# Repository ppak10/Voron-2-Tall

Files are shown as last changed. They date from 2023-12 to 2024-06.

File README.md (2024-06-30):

# Voron 2 Tall

<!-- <div align="center">
  <img src="./images/placeholder.JPEG" width="500px">
</div> -->

Collection of files for building custom Voron 2.4 with a build volume of 350 mm
x 350 mm x 930 mm (13.78 in x 13.78 in x 36.61 in) modified from the base LDO
Voron 2.4 Kit. 

## Mods
- [Cable Port Flush Mount Skirt](https://mods.vorondesign.com/details/3vEc5I965u0puzAmz9DqvA) - [ppak10](https://github.com/ppak10)
- [Enclosed Z-Chain Guide](https://mods.vorondesign.com/details/4mSRcdfNCvSq6nsRHETw) - [ppak10](https://github.com/ppak10)
- [Nevermore Micro](https://github.com/nevermore3d/Nevermore_Micro) - [nevermore3d](https://github.com/nevermore3d)
- [Purge Bucket](https://github.com/VoronDesign/VoronUsers/tree/main/orphaned_mods/edwardyeeks/Decontaminator_Purge_Bucket_%26_Nozzle_Scrubber) - [edwardyeeks](https://github.com/edwardyeeks)
- Umbilical Mount (Choose One) 
  - [Rear Umbilical](https://mods.vorondesign.com/details/ho9WEyf6msbGKhTbtM59mQ) - [Minsekt](https://github.com/Minsekt)
  - [PG7 Umbilical Mount](https://www.printables.com/model/312008-voron-24-a-drive-pg7-umbilical-mount) - [jphalip](https://www.printables.com/@jphalip)

- [Y Endstop Relocation](https://mods.vorondesign.com/details/ho9WEyf6msbGKhTbtM59mQ) - [Minsekt](https://github.com/Minsekt)

## Canbus Setup

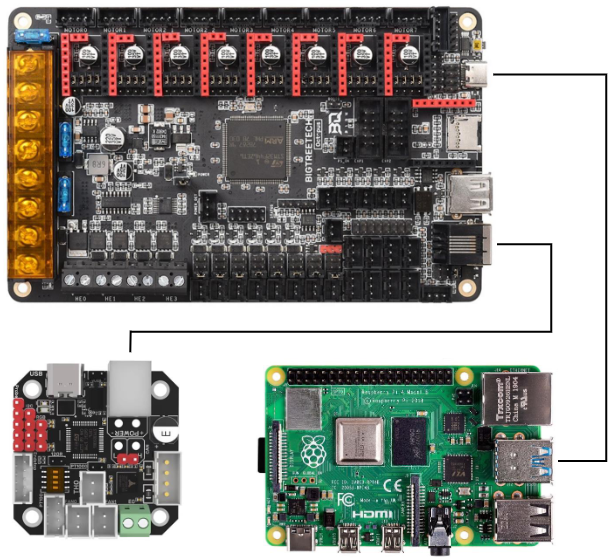
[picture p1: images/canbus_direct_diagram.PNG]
Canbus Direct Diagram


I mostly followed the steps outlined in this [forum post](https://www.teamfdm.com/forums/topic/672-how-to-use-can-toolhead-boards-connected-directly-to-octopus-octopus-pro-on-canboot/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) to connect EBB directly to
Octopus.

More specifically, I followed the guide this guide that was attached.

[**How to Use CAN Toolhead Boards Connected Directly to Octopus / Octopus Pro on CanBoot**](Manuals/Canbus/How%20to%20Use%20CAN%20Toolhead%20Boards%20Connected%20Directly%20to%20Octopus.pdf)

### Notes
1. CanBoot has updated name to Katapult but instructions in manual should still work.
2. If `can0` doesn't automatically show up in `ifconfig` so this command should solve that:
    ```bash
    sudo ip link set can0 up type can bitrate 250000
    sudo ip link set can0 txqueuelen 128
    ```
3. Make sure the high and low can wires are set correctly otherwise ebb will not show up properly.

### Troubleshooting 
- [CANBus_Query.py not returning EBB36’s UUID. Setup: Pi 4, Octopus v1.1, EBB36 v1.2](https://klipper.discourse.group/t/canbus-query-py-not-returning-ebb36s-uuid-setup-pi-4-octopus-v1-1-ebb36-v1-2/8464)
- [MCU timer too close error](https://klipper.discourse.group/t/help-with-troubleshooting-mcu-timer-too-close-error/15913/18)
- [EBB_CAN](https://github.com/EricZimmerman/VoronTools/blob/main/EBB_CAN.md)

## Toolhead (Dragon Burner 2.85 mm)
[Dragon Burner V8](https://github.com/chirpy2605/voron/tree/main/V0/Dragon_Burner)
toolhead is used as the base for mounting an
[Orbiter F2.85 mm](https://www.orbiterprojects.com/orbiter-f2-85/) extruder and
[V6 All-Metal HotEnd](https://e3d-online.com/products/v6-all-metal-hotend?variant=40923457519675).

### Notes
1. Some printed component will need some light sanding to fit together properly.
    - Be gentle with the fan components, they can break easily.
2. Make sure to calibrate E-steps as the default settings will most likely result in under-extrusion.
    - Here's a [good guide](https://ellis3dp.com/Print-Tuning-Guide/articles/extruder_calibration.html) with instructions to calibrate E-steps
    - General Formula: `new_rotation_distance = previous_rotation_distance * (actual_extrude_distance / 100)`

### Extruder


- [Orbiter F2.85 mm Files](https://www.thingiverse.com/thing:4860182)

### Hotend
- [How To: Successfully Assemble an E3D v6 All-Metal HotEnd](https://www.matterhackers.com/articles/how-to-assemble-an-e3d-v6-all-metal-hotend)

## Other Useful Links

### LDO Docs
- [Wiring Guide](https://docs.ldomotors.com/en/voron/voron2/wiring_guide_rev_c)
- [Printed Parts](https://docs.ldomotors.com/en/voron/voron2/printed_part_guide_rev_c)

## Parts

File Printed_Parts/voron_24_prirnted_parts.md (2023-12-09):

### Voron 2.4 Printed Parts List
https://gist.github.com/cmidgley/10423bbae72dacb02c46926f60acb7d2

List of parts to print for [Voron 2.4](https://github.com/VoronDesign/Voron-2) organized by the [Assembly Manuals](https://github.com/VoronDesign/Voron-2/blob/Voron2.4/Docs/2.4_Assembly_Manual.pdf) order of assembly, allowing for just-in-time printing of parts while building the printer.  Configuration is standard Voron 2.4 (Afterburner Direct Feed, DIN rail mounts) with choices for E3D, Dragon or Mosquito hot ends on a 250mm, 300mm or 350mm frame.  No parts for the drag chain are included, as often these are purchased parts rather than printed.

Names of the sections (such as `Gantry/X_Axis/XY Joints`) match the name of the [STL directory](https://github.com/VoronDesign/Voron-2/tree/Voron2.4/STLs/VORON2.4) that contains the prints.  Note that Voron Design uses filenames starting with `[a]_` at the start of a filename to indicate parts that can be printed in an accent color.

_Credit to [krobertson](https://gist.github.com/krobertson/adfd96689e8b66e7e122705c9ac6bb21) for making a Gist of all parts. This Gist is a modified version of that list, organized by order of assembly, removed parts that don't need printing, identified parts that are optional or specific to a build, and fixed a few incorrect part listings._

--------------------------------------------------------------------------------

### Frame (page 10)

#### [Tools](https://github.com/VoronDesign/Voron-2/tree/Voron2.4/STLs/VORON2.4/Tools)

```
[  ]  [  ]   rail_installation_guide_center_x2.stl
```

--------------------------------------------------------------------------------

### Z Drive Assembly (page 18)

#### [Z_Drive](https://github.com/VoronDesign/Voron-2/tree/Voron2.4/STLs/VORON2.4/Z_Drive)

```
[  ]  [  ]   [a]_belt_tensioner_a_x2.stl
[  ]  [  ]   [a]_belt_tensioner_b_x2.stl
[  ]  [  ]   [a]_z_drive_baseplate_a_x2.stl
[  ]  [  ]   [a]_z_drive_baseplate_b_x2.stl
[  ]  [  ]   z_drive_main_a_x2.stl
[  ]  [  ]   z_drive_main_b_x2.stl
[  ]  [  ]   z_drive_retainer_a_x2.stl
[  ]  [  ]   z_drive_retainer_b_x2.stl
[  ]  [  ]   z_motor_mount_a_x2.stl
[  ]  [  ]   z_motor_mount_b_x2.stl
```

#### [Z_Idlers](https://github.com/VoronDesign/Voron-2/tree/Voron2.4/STLs/VORON2.4/Z_Idlers)

_There are two different GT20 20T pully files; only one set of them should be printed_

```
[  ]  [  ]  [  ]  [  ]   [a]_z_tensioner_x4_6mm.stl <- select one vvv (6mm pully)
[  ]  [  ]  [  ]  [  ]   [a]_z_tensioner_x4_9mm.stl <- select one ^^^ (9mm pully)
[  ]  [  ]               z_tensioner_bracket_a_x2.stl
[  ]  [  ]               z_tensioner_bracket_b_x2.stl
```

#### [Z_Endstop](https://github.com/VoronDesign/Voron-2/tree/Voron2.4/STLs/VORON2.4/Z_Endstop)

```
[  ]   nozzle_probe.stl
```

--------------------------------------------------------------------------------

### AB Drive Modules (page 38)

#### [Gantry/Front_Idlers](https://github.com/VoronDesign/Voron-2/tree/Voron2.4/STLs/VORON2.4/Gantry/Front_Idlers)

```
[  ]   [a]_tensioner_left.stl
[  ]   [a]_tensioner_right.stl
[  ]   front_idler_left_lower.stl
[  ]   front_idler_left_upper.stl
[  ]   front_idler_right_lower.stl
[  ]   front_idler_right_upper.stl
```

#### [Gantry/AB_Drive_Units](https://github.com/VoronDesign/Voron-2/tree/Voron2.4/STLs/VORON2.4/Gantry/AB_Drive_Units)

```
[  ]         [a]_cable_cover.stl
[  ]  [  ]   [a]_z_chain_retainer_bracket_x2.stl
[  ]         a_drive_frame_lower.stl
[  ]         a_drive_frame_upper.stl
[  ]         b_drive_frame_lower.stl
[  ]         b_drive_frame_upper.stl
```

--------------------------------------------------------------------------------

### Gantry (page 46)

#### [Gantry/X_Axis/XY Joints](https://github.com/VoronDesign/Voron-2/tree/Voron2.4/STLs/VORON2.4/Gantry/X_Axis/XY_Joints)

_Select one endstop_pod_* , and one xy_joint_cable_bridge_* depending on your hardware kit_

```
[  ]   [a]_endstop_pod_hall_effect.stl <- select one vvv (hall effect XY endstops)
[  ]   [a]_endstop_pod_microswitch.stl <- select one ^^^ (microswitch XY endstops)
[  ]   [a]_xy_joint_cable_bridge_generic.stl <= select one vvv (generic drag chain)
[  ]   [a]_xy_joint_cable_bridge_igus.stl    <= select one ^^^ (igus drag chain)
[  ]   xy_joint_left_lower.stl
[  ]   xy_joint_left_upper.stl
[  ]   xy_joint_right_lower.stl
[  ]   xy_joint_right_upper.stl
```

#### [Gantry](https://github.com/VoronDesign/Voron-2/tree/Voron2.4/STLs/VORON2.4/Gantry)

```
[  ]  [  ]  [  ]  [  ]   [a]_z_belt_clip_lower_x4.stl
[  ]  [  ]  [  ]  [  ]   [a]_z_belt_clip_upper_x4.stl
[  ]                     z_chain_bottom_anchor.stl
[  ]                     z_chain_guide.stl              <-- Not in CAD or documentation
```

--------------------------------------------------------------------------------

### Afterburner (page 58)

#### [Gantry/X_Axis/X Carriage](https://github.com/VoronDesign/Voron-2/tree/Voron2.4/STLs/VORON2.4/Gantry/X_Axis/X_Carriage)

```
[  ]  [  ]   [a]_belt_clamp_x2.stl
[  ]         [a]_blower_housing_front.stl
[  ]         blower_housing_rear.stl
[  ]         hotend_fan_mount.stl
[  ]         probe_retainer_bracket.stl
[  ]         x_carriage_frame_left.stl
[  ]         x_carriage_frame_right.stl
[  ]         x_carriage_pivot_block.stl
```

#### [Gantry/X_Axis/X Carriage/Printheads/E3D V6](https://github.com/VoronDesign/Voron-2/tree/Voron2.4/STLs/VORON2.4/Gantry/X_Axis/X_Carriage/Printheads/E3D_V6)

_Select only one printhead; this is for E3D_

```
[  ]   printhead_front_e3dv6.stl
[  ]   printhead_rear_e3dv6.stl
```

#### [Gantry/X_Axis/X Carriage/Printheads/Slice Mosquito](https://github.com/VoronDesign/Voron-2/tree/Voron2.4/STLs/VORON2.4/Gantry/X_Axis/X_Carriage/Printheads/Slice_Mosquito)

_Select only one printhead; this is for Slice Mosquito_

```
[  ]   printhead_front_mosquito.stl
[  ]   printhead_rear_mosquito.stl
```

#### [Gantry/X_Axis/X Carriage/Printheads/TriangleLab Dragon](https://github.com/VoronDesign/Voron-2/tree/Voron2.4/STLs/VORON2.4/Gantry/X_Axis/X_Carriage/Printheads/TriangleLab_Dragon)

_Select only one printhead; this is for Phaetus Dragon_

```
[  ]   printhead_front_dragon.stl
[  ]   printhead_rear_dragon.stl
```

#### [Gantry/X_Axis/X Carriage/Direct Feed](https://github.com/VoronDesign/Voron-2/tree/Voron2.4/STLs/VORON2.4/Gantry/X_Axis/X_Carriage/Direct_Feed)

_Select the chain anchor (generic or igus) that matches your drag chain choice_ 

```
[  ]   [a]_connector_cover.stl
[  ]   [a]_guidler.stl
[  ]   [a]_latch.stl
[  ]   chain_anchor_generic.stl <-- select one vvv (generic drag chain)
[  ]   chain_anchor_igus.stl    <-- select one ^^^ (igus drag chain)
[  ]   extruder_body.stl
[  ]   extruder_motor_plate.stl
[  ]   latch_shuttle.stl
```

--------------------------------------------------------------------------------

### Belting Z Drive (page 78)

#### [Gantry/Z_Joints](https://github.com/VoronDesign/Voron-2/tree/Voron2.4/STLs/VORON2.4/Gantry/Z_Joints)

```
[  ]  [  ]  [  ]  [  ]   z_joint_lower_x4.stl
[  ]                     z_joint_upper_hall_effect.stl <-- if using hall effect XY
[  ]  [  ]  [  ]  [  ]   z_joint_upper_x4.stl <-- use x3 if using hall effect XY
```

--------------------------------------------------------------------------------

###  LCD Module (page 82)

#### [Electronics_Compartment/LCD_Module](https://github.com/VoronDesign/Voron-2/tree/Voron2.4/STLs/VORON2.4/Electronics_Compartment/LCD_Module)

```
[  ]   [a]_mini12864_case_hinge.stl
[  ]   mini12864_case_front.stl
[  ]   mini12864_case_rear.stl
[  ]   mini12864_spacer.stl
```

--------------------------------------------------------------------------------

### Skirts (page 86)

#### [Electronics_Compartment/Plug_Panel](https://github.com/VoronDesign/Voron-2/tree/Voron2.4/STLs/VORON2.4/Electronics_Compartment/Plug_Panel)

```
[  ]   plug_panel_filtered_mains.stl
```

#### [Skirts](https://github.com/VoronDesign/Voron-2/tree/Voron2.4/STLs/VORON2.4/Skirts)

```
[  ]  [  ]   [a]_60mm_fan_blank_insert_x2.stl
[  ]  [  ]   [a]_belt_guard_a_x2.stl
[  ]  [  ]   [a]_belt_guard_b_x2.stl
[  ]  [  ]   side_fan_support_x2.stl
```

#### [250](https://github.com/VoronDesign/Voron-2/tree/Voron2.4/STLs/VORON2.4/Skirts/250)

_Use these skirts when printing a 250mm frame_

```
[  ]  [  ]   front_rear_skirt_a_250_x2.stl
[  ]  [  ]   front_rear_skirt_b_250_x2.stl
[  ]  [  ]   side_skirt_a_250_x2.stl
[  ]  [  ]   side_skirt_b_250_x2.stl
```

#### [300](https://github.com/VoronDesign/Voron-2/tree/Voron2.4/STLs/VORON2.4/Skirts/300)

_Use these skirts when printing a 300mm frame_

```
[  ]  [  ]   front_rear_skirt_a_300_x2.stl
[  ]  [  ]   front_rear_skirt_b_300_x2.stl
[  ]  [  ]   side_skirt_a_300_x2.stl
[  ]  [  ]   side_skirt_b_300_x2.stl
```

#### [350](https://github.com/VoronDesign/Voron-2/tree/Voron2.4/STLs/VORON2.4/Skirts/350)

_Use these skirts when printing a 350mm frame_

```
[  ]  [  ]   front_rear_skirt_a_350_x2.stl
[  ]  [  ]   front_rear_skirt_b_350_x2.stl
[  ]  [  ]   side_skirt_a_350_x2.stl
[  ]  [  ]   side_skirt_b_350_x2.stl
```

--------------------------------------------------------------------------------

### Panels (page 94)

#### [Panel_Mounting/Front_Doors](https://github.com/VoronDesign/Voron-2/tree/Voron2.4/STLs/VORON2.4/Panel_Mounting/Front_Doors)

```
[  ]  [  ]  [  ]  [  ]   door_hinge_x4.stl
[  ]  [  ]               handle_a_x2.stl
[  ]  [  ]               handle_b_x2.stl
[  ]  [  ]               latch_x2.stl
```

#### [Panel_Mounting](https://github.com/VoronDesign/Voron-2/tree/Voron2.4/STLs/VORON2.4/Panel_Mounting)

```
[  ]  [  ]  [  ]  [  ]                                                   bottom_panel_clip_x4.stl
[  ]  [  ]                                                               bottom_panel_hinge_x2.stl
[  ]  [  ]  [  ]  [  ]  [  ]  [  ]  [  ]  [  ]  [  ]  [  ]  [  ]  [  ]   corner_panel_clip_3mm_x12.stl  <-- 3mm no foam, 6mm w/foam
[  ]  [  ]  [  ]  [  ]                                                   corner_panel_clip_6mm_x4.stl   <-- print either the 3mm or
[  ]  [  ]  [  ]  [  ]  [  ]  [  ]  [  ]  [  ]  [  ]  [  ]  [  ]  [  ]   midspan_panel_clip_3mm_x12.stl <-- the 6mm set 
[  ]  [  ]  [  ]                                                         midspan_panel_clip_6mm_x3.stl  <--  
[  ]  [  ]                                                               z_belt_cover_a_x2.stl
[  ]  [  ]                                                               z_belt_cover_b_x2.stl
```

--------------------------------------------------------------------------------

### Spool Holder (page 102)

#### [Spool_Management](https://github.com/VoronDesign/Voron-2/tree/Voron2.4/STLs/VORON2.4/Spool_Management)

```
[  ]   bowen_retainer.stl
[  ]   spool_holder.stl
```

--------------------------------------------------------------------------------

### Exhaust Filter (page 106)

#### [Exhaust_Filter](https://github.com/VoronDesign/Voron-2/tree/Voron2.4/STLs/VORON2.4/Exhaust_Filter)

```
[  ]         [a]_filter_access_cover.stl
[  ]  [  ]   [a]_exhaust_filter_mount_x2.stl
[  ]         exhaust_filter_grill.stl
[  ]         exhaust_filter_housing.stl
```

--------------------------------------------------------------------------------

### Electronics Mounting (page 112)

#### [Electronics_Compartment/DIN_Brackets](https://github.com/VoronDesign/Voron-2/tree/Voron2.4/STLs/VORON2.4/Electronics_Compartment/DIN_Brackets)

_There are a number of different brackets here depending on your electronics selection._

```
[  ]  [  ]         duet_duex_bracket_x2.stl
[  ]               lrs_psu_bracket_clip.stl
[  ]  [  ]  [  ]   pcb_din_clip_x3.stl
[  ]  [  ]         ramps_bracket_x2.stl
[  ]               raspberrypi_bracket.stl
[  ]               rs25_psu_bracket_clip.stl
[  ]  [  ]         skr_1.3_bracket_x2.stl
[  ]  [  ]         skr_mini_e2_bracket_x2.stl
[  ]  [  ]         skr_mini_e3_bracket_x2.stl
```

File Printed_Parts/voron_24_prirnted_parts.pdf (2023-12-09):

voron_24_prirnted_parts.md | 2023-12-09

### Voron 2.4 Printed Parts List

https://gist.github.com/cmidgley/10423bbae72dacb02c46926f60acb7d2

List of parts to print for Voron 2.4 (https://github.com/VoronDesign/Voron-2) organized by the Assembly Manuals (https://github.com/VoronDesign/Voron-2/blob/Voron2.4/Docs/2.4_Assembly_Manual.pdf) order of assembly, allowing for just-in-time printing of parts while building the printer. Configuration is standard Voron 2.4 (Afterburner Direct Feed, DIN rail mounts) with choices for E3D, Dragon or Mosquito hot ends on a 250mm, 300mm or 350mm frame. No parts for the drag chain are included, as often these are purchased parts rather than printed.

Names of the sections (such as Gantry/X_Axis/XY Joints) match the name of the STL directory (https://github.com/VoronDesign/Voron-2/tree/Voron2.4/STLs/VORON2.4) that contains the prints. Note that Voron Design uses filenames starting with [a]_ at the start of a filename to indicate parts that can be printed in an accent color.

Credit to krobertson (https://gist.github.com/krobertson/adfd96689e8b66e7e122705c9ac6bb21) for making a Gist of all parts. This Gist is a modified version of that list, organized by

order of assembly, removed parts that don't need printing, identified parts that are optional or specific to a

build, and fixed a few incorrect part listings.

### Frame (page 10)

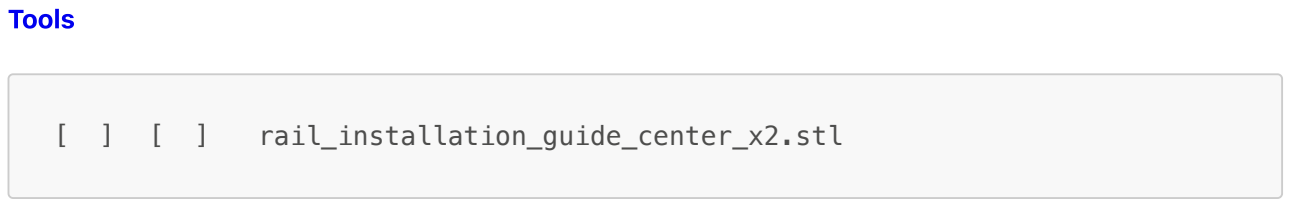
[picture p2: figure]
Tools; rail_installation_guide_center_x2.stl

### Z Drive Assembly (page 18)

Z_Drive (https://github.com/VoronDesign/Voron-2/tree/Voron2.4/STLs/VORON2.4/Z_Drive)

[ ] [ ] | [a]_belt_tensioner_a_x2.stl
[ ] [ ] | [a]_belt_tensioner_b_x2.stl
[ ] [ ] | [a]_z_drive_baseplate_a_x2.stl
[ ] [ ] | [a]_z_drive_baseplate_b_x2.stl
[ ] [ ] | z_drive_main_a_x2.stl
[ ] [ ] | z_drive_main_b_x2.stl
[ ] [ ] | z_drive_retainer_a_x2.stl
[ ] [ ] | z_drive_retainer_b_x2.stl
[ ] [ ] | z_motor_mount_a_x2.stl
[ ] [ ] | z_motor_mount_b_x2.stl

Z_Idlers (https://github.com/VoronDesign/Voron-2/tree/Voron2.4/STLs/VORON2.4/Z_Idlers)

There are two different GT20 20T pully files; only one set of them should be printed

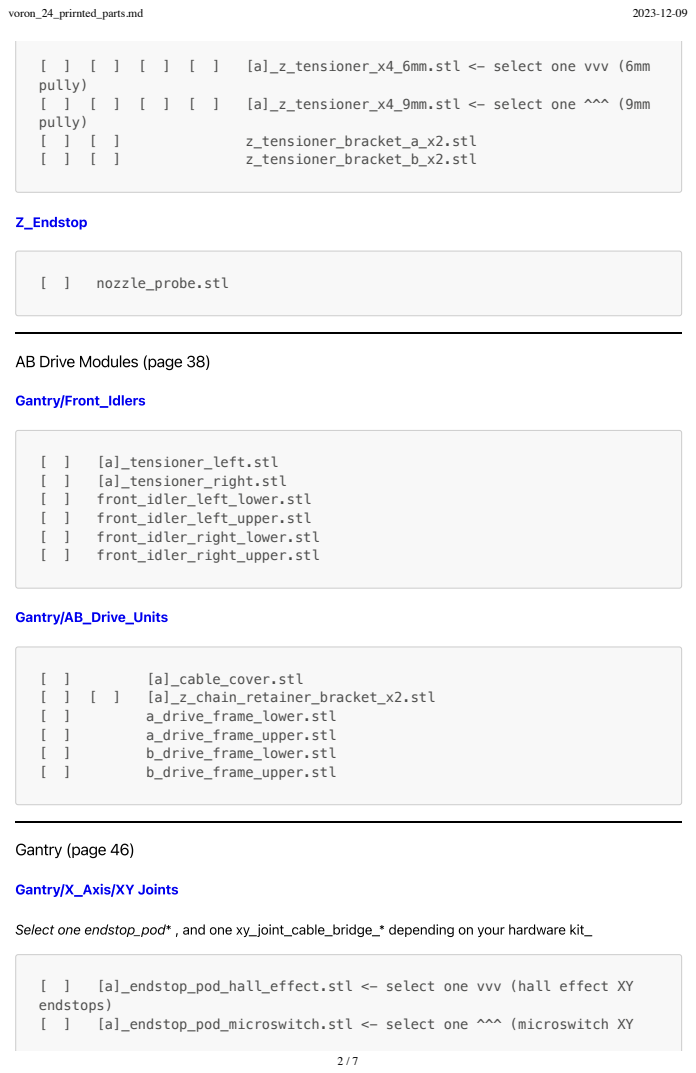
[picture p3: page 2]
[a]_z_tensioner_x4_6mm.stl <- select one vvv (6mm; pully); [a]_z_tensioner_x4_9mm.stl <- select one ^^^ (9mm; z_tensioner_bracket_a_x2.stl; z_tensioner_bracket_b_x2.stl; Z_Endstop; nozzle_probe.stl; Gantry/Front_Idlers; [a]_tensioner_left.stl; [a]_tensioner_right.stl; front_idler_left_lower.stl; front_idler_left_upper.stl; front_idler_right_lower.stl; front_idler_right_upper.stl; Gantry/AB_Drive_Units; [a]_cable_cover.stl; [a]_z_chain_retainer_bracket_x2.stl; a_drive_frame_lower.stl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

AB Drive Modules (page 38)

Gantry/X_Axis/XY Joints (https://github.com/VoronDesign/Voron-2/tree/Voron2.4/STLs/VORON2.4/Gantry/X_Axis/XY_Joints)

Select one endstop_pod* , and one xy_joint_cable_bridge_* depending on your hardware kit_

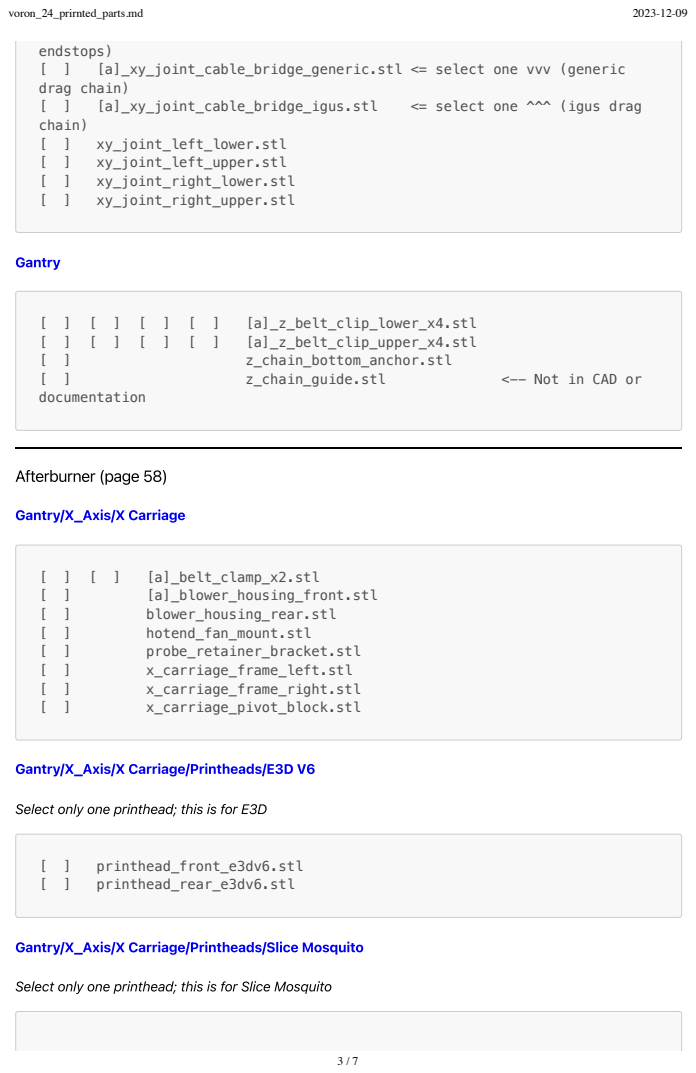
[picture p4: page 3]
endstops); [a]_xy_joint_cable_bridge_generic.stl <= select one vvv (generic; drag chain); [a]_xy_joint_cable_bridge_igus.stl; <= select one ^^^ (igus drag; chain); xy_joint_left_lower.stl; xy_joint_left_upper.stl; xy_joint_right_lower.stl; xy_joint_right_upper.stl; Gantry; [a]_z_belt_clip_lower_x4.stl; [a]_z_belt_clip_upper_x4.stl; z_chain_bottom_anchor.stl; z_chain_guide.stl; <-- Not in CAD or; documentation; Afterburner (page 58); Gantry/X_Axis/X Carriage; [a]_belt_clamp_x2.stl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

Gantry/X_Axis/X Carriage/Printheads/E3D V6 (https://github.com/VoronDesign/Voron-2/tree/Voron2.4/STLs/VORON2.4/Gantry/X_Axis/X_Carriage/Printheads/E3D_V6)

Select only one printhead; this is for E3D

Gantry/X_Axis/X Carriage/Printheads/Slice Mosquito (https://github.com/VoronDesign/Voron-2/tree/Voron2.4/STLs/VORON2.4/Gantry/X_Axis/X_Carriage/Printheads/Slice_Mosquito)

Select only one printhead; this is for Slice Mosquito

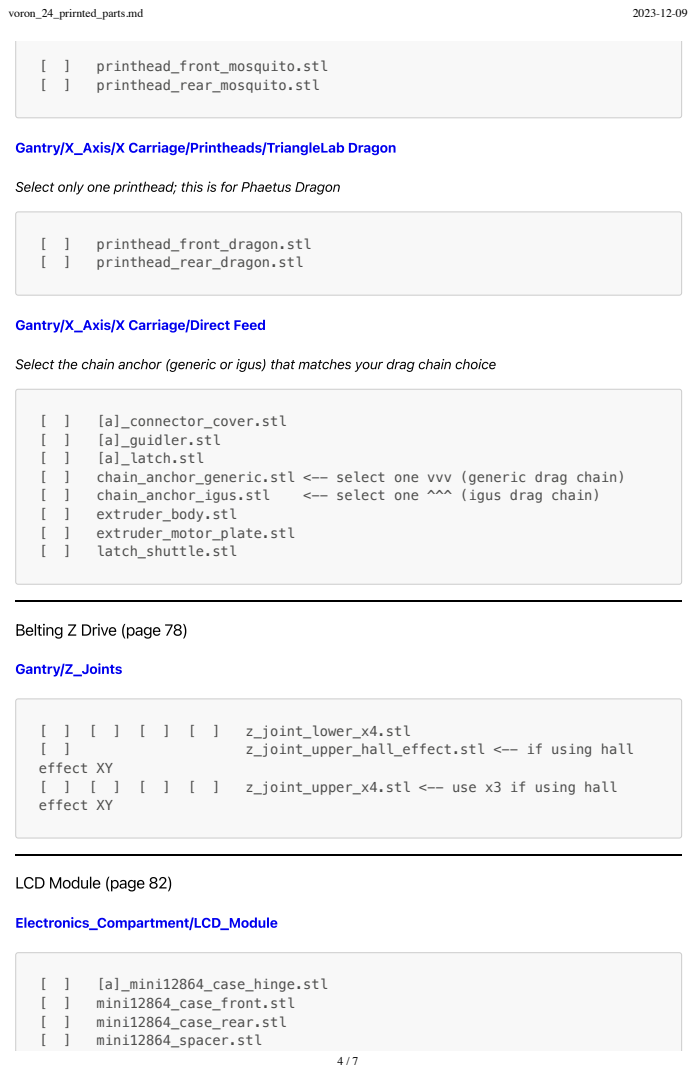
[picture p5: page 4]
printhead_front_mosquito.stl; printhead_rear_mosquito.stl; printhead_front_dragon.stl; printhead_rear_dragon.stl; [a]_connector_cover.stl; [a]_guidler.stl; [a]_latch.stl; chain_anchor_generic.stl <-- select one vvv (generic drag chain); chain_anchor_igus.stl; <-- select one ^^^ (igus drag chain); extruder_body.stl; extruder_motor_plate.stl; latch_shuttle.stl; Gantry/Z_Joints; z_joint_lower_x4.stl; z_joint_upper_hall_effect.stl <-- if using hall; effect XY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

Gantry/X_Axis/X Carriage/Printheads/TriangleLab Dragon (https://github.com/VoronDesign/Voron-2/tree/Voron2.4/STLs/VORON2.4/Gantry/X_Axis/X_Carriage/Printheads/TriangleLab_Dragon)

Select only one printhead; this is for Phaetus Dragon

Gantry/X_Axis/X Carriage/Direct Feed (https://github.com/VoronDesign/Voron-2/tree/Voron2.4/STLs/VORON2.4/Gantry/X_Axis/X_Carriage/Direct_Feed)

Select the chain anchor (generic or igus) that matches your drag chain choice

Belting Z Drive (page 78)

LCD Module (page 82)

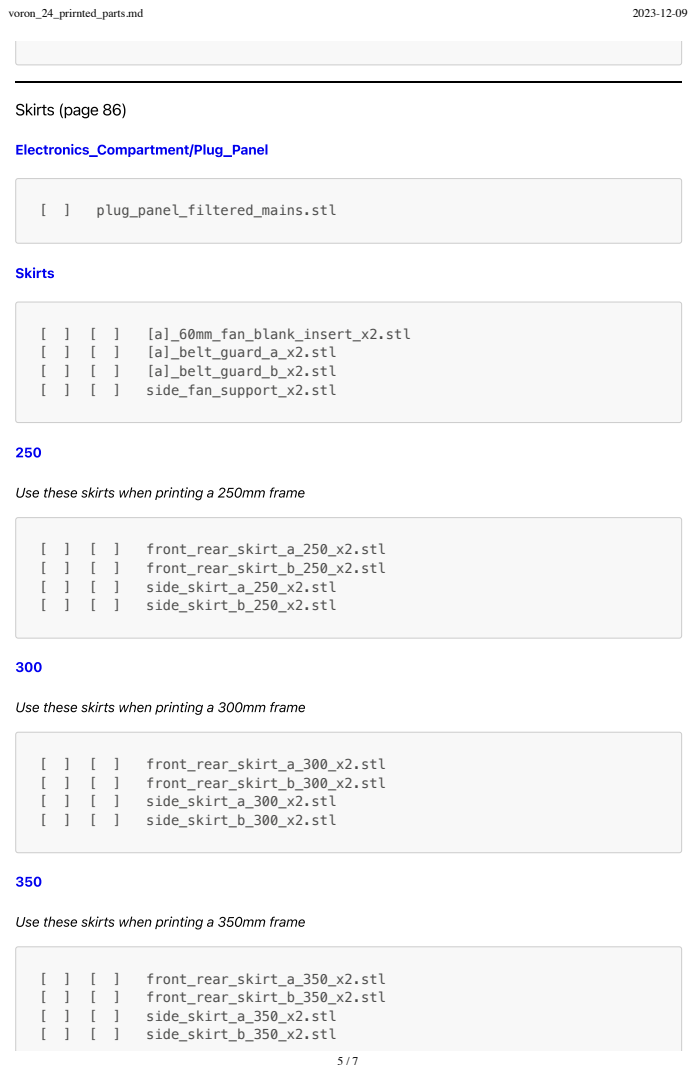
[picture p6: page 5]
Skirts (page 86); Electronics_Compartment/Plug_Panel; plug_panel_filtered_mains.stl; Skirts; [a]_60mm_fan_blank_insert_x2.stl; [a]_belt_guard_a_x2.stl; [a]_belt_guard_b_x2.stl; side_fan_support_x2.stl; front_rear_skirt_a_250_x2.stl; front_rear_skirt_b_250_x2.stl; side_skirt_a_250_x2.stl; side_skirt_b_250_x2.stl; front_rear_skirt_a_300_x2.stl; front_rear_skirt_b_300_x2.stl; side_skirt_a_300_x2.stl; side_skirt_b_300_x2.stl; front_rear_skirt_a_350_x2.stl; front_rear_skirt_b_350_x2.stl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

Use these skirts when printing a 250mm frame

Use these skirts when printing a 300mm frame

Use these skirts when printing a 350mm frame

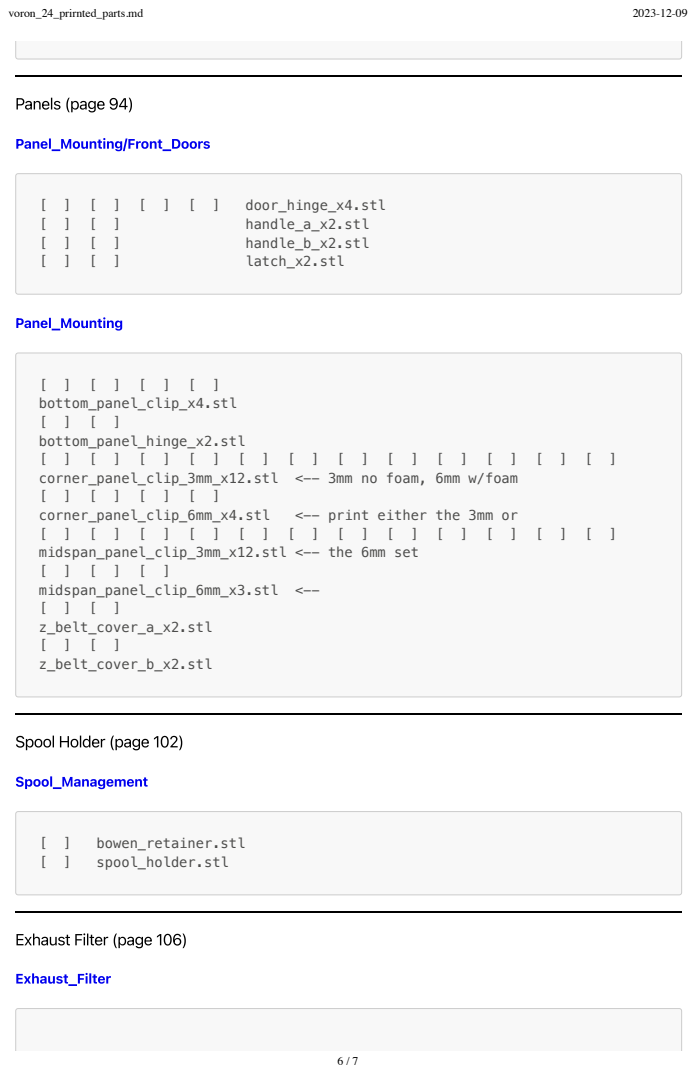
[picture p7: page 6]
Panels (page 94); Panel_Mounting/Front_Doors; door_hinge_x4.stl; handle_a_x2.stl; handle_b_x2.stl; latch_x2.stl; Panel_Mounting; [ ] [ ] [ ] [ ] bottom_panel_clip_x4.stl [ ] [ ] bottom_panel_hinge_x2.stl [ ] [ ] [ ] [ ] [ ] [ ] [ ] [ ] [ ] [ ] [ ] [ ] corner_panel_clip_3mm_x12.stl <-- 3mm no foam, 6mm w/foam [ ] [ ] [ ] [ ]; corner_panel_clip_6mm_x4.stl; <-- print either the 3mm or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

Spool Holder (page 102)

Exhaust Filter (page 106)

[ ] | [a]_filter_access_cover.stl
[ ] [ ] | [a]_exhaust_filter_mount_x2.stl
[ ] | exhaust_filter_grill.stl
[ ] | exhaust_filter_housing.stl

### Electronics Mounting (page 112)

Electronics_Compartment/DIN_Brackets (https://github.com/VoronDesign/Voron-2/tree/Voron2.4/STLs/VORON2.4/Electronics_Compartment/DIN_Brackets)

There are a number of different brackets here depending on your electronics selection.

[ ] [ ] | duet_duex_bracket_x2.stl
[ ] | lrs_psu_bracket_clip.stl
[ ] [ ] [ ] | pcb_din_clip_x3.stl
[ ] [ ] | ramps_bracket_x2.stl
[ ] | raspberrypi_bracket.stl
[ ] | rs25_psu_bracket_clip.stl
[ ] [ ] | skr_1.3_bracket_x2.stl
[ ] [ ] | skr_mini_e2_bracket_x2.stl
[ ] [ ] | skr_mini_e3_bracket_x2.stl

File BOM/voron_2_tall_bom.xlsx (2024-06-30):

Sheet: 1_custom_kit
1. LDO Kit + Custom Materials
Build Volume: 350mm x 350mm x (850mm to 930mm)
Frame Dimensions: 510mm x 510mm x 1130mm
 |  |  |  | Quantity |  |  | Subtotals
Description | Min Qty | Notes | Price | Desired | Ordered | Paid | Expected | Remaining | Link
LDO Voron 2.4 R2 (Rev C) 3D Printer Kit | 1 | Base Voron 2.4 Materials | $1449.00 | 1 | 0 | $0.00 | $1449.00 | $1449.00 | https://www.matterhackers.com/store/l/voron-design-corexy-fdm-3d-printer
M3-0.5 x 8mm Socket Head Cap Screws Bolts | 100 | Pack of 100 | $5.99 | 1 | 0 | $0.00 | $5.99 | $5.99 | https://www.amazon.com/dp/B09B2CGW12?psc=1&ref=ppx_yo2ov_dt_b_product_details
M3 Post-install T-nut | 163 | 20-m3 100pcs | $12.88 | 2 | 0 | $0.00 | $25.76 | $25.76 | https://www.aliexpress.us/item/2251832618848960.html?sk=KUHCwnu4&terminal_id=77b480c9601746d1be2247846d74a043
GT2 Open Belt LL-2GT-9 (9mm wide) - 8M | 1 | LDO Kit already includes 5.9M | $30.91 | 1 | 0 | $0.00 | $30.91 | $30.91 | https://www.aliexpress.us/item/2251832667244886.html?gatewayAdapt=glo2usa4itemAdapt
Linear Rail MGN9H 1000mm | 4 |  | $66 | 4 | 0 | $0.00 | $264.00 | $264.00 | https://3dprintingusa.com/products/9mm-linear-rail-1000mm-with-one-mgn9h-block
Misumi HFSB5-2020-1130-LCP-RCP | 4 | Holes 10mm from each end | $25.97 | 4 | 0 | $0.00 | $103.88 | $103.88 | https://us.misumi-ec.com/vona2/detail/110302683830/?Inch=0&Tab=preview
PTFE Tube (4mm OD 3mm ID) - 1000mm | 1 | 9.84 ft | $8.99 | 1 | 0 | $0.00 | $8.99 | $8.99 | https://www.amazon.com/gp/product/B07B8CK8L9/ref=ppx_yo_dt_b_asin_title_o00_s00?ie=UTF8&th=1
IGUS E2-15-10-028-0 Chain (1145mm [3.76ft]) | 1 | Extra (60) Chain Links for height | $46.44 | 1 | 0 | $0.00 | $46.44 | $46.44 | https://www.igus.com/iPro/iPro_01_0002_0015_USen.htm?ArtNr=E2-15-10-028-0&c=US&l=en
IGUS E2-150-10-12PZ Chain Ends (set) | 1 |  | $6.12 | 1 | 0 | $0.00 | $6.12 | $6.12 | https://www.igus.com/iPro/iPro_01_0002_0015_USen.htm?ArtNr=E2-15-10-028-0&c=US&l=en
Clear Acrylic Sheet 24" x 48" x 1/8"(4 Pack) | 1 | Side and Back Panels (483x1103x3 mm) | $139.80 | 1 | 0 | $0.00 | $139.80 | $139.80 | https://www.amazon.com/dp/B0BBQ7683N/ref=twister_B0BBQ7G8WZ?_encoding=UTF8&th=1
 |  | Door Panels (241.5x1103x3 mm) |  |  |  | $0.00
 |  |  |  |  |  | $0.00 | $2080.89 | $2080.89
Panels
Buildplate

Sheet: 2_wiring
2. Wiring
Necessary Materials
Option 1: Extended LDO Wiring
Option 2: Canbus (Recommended)
Necessary Materials |  |  |  | Quantity |  |  | Subtotals
Description | Min Qty | Notes | Price | Desired | Ordered | Paid | Expected | Remaining | Link
Female 4P to Male 4P Motor Extension Wire | 2 | For A/B stepper and limit (Pack of 2) | $12.99 | 2 | 0 | $0.00 | $25.98 | $25.98 | https://www.amazon.com/dp/B098J4MM3G?psc=1&ref=ppx_yo2ov_dt_b_product_details
Heat Shrink Tubing & Sleeves Pre-Cut Multi-Colored Heat Shrink Pack | 1 | Various heatshrink for extenders | $9.95 | 1 | 0 | $0.00 | $9.95 | $9.95 | https://www.mouser.com/ProductDetail/485-4559
 |  |  |  |  |  | $0.00 | $35.93 | $35.93
Option 1: Extended LDO Wiring |  |  |  | Quantity |  |  | Remaining Subtotals
Description | Min Qty | Notes | Price | Desired | Ordered | Paid | Required | Overall | Link
MicroFit3 Female Pin | 28 | For 20 - 24 AWG | $0.08 | 100 | 0 | $0.00 | $8.30 | $8.30 | https://www.mouser.com/ProductDetail/538-43030-0001-CT
MicroFit3 Connector Plug 14 Position | 2 | LDO toolhead plug | $1.02 | 2 | 0 | $0.00 | $2.04 | $2.04 | https://www.mouser.com/ProductDetail/538-43025-1410
Headers & Wire Housings PLUG FREE HNG 2P SINGLE ROW | 1 | Stealthburner RGB Extender (Female) | $0.38 | 2 | 0 | $0.00 | $0.76 | $0.76 | https://www.mouser.com/ProductDetail/Molex/43640-0201?qs=HlEFOAM0q6WaYhPmKKx%252BhQ%3D%3D
Headers & Wire Housings RECEPTACLE 2 POS SINGLE ROW | 1 | Stealthburner RGB Extender (Male) | $0.40 | 2 | 0 | $0.00 | $0.80 | $0.80 | https://www.mouser.com/ProductDetail/Molex/43645-0200?qs=4XSMV6Twtb2TZ7elJDViLw%3D%3D
Headers & Wire Housings 14CKT PLUG HSG FREE HANGING DR | 1 | Stealthburner Extender (Female) | $0.86 | 2 | 0 | $0.00 | $1.72 | $1.72 | https://www.mouser.com/ProductDetail/538-43020-1401
Headers & Wire Housings MicroFit Recep HSG DR 14Ckt GW BLK | 1 | Stealthburner Extender (Male) | $1.02 | 2 | 0 | $0.00 | $2.04 | $2.04 | https://www.mouser.com/ProductDetail/538-43025-1410
Headers & Wire Housings MALE 20-24 AWG BULK tin | 16 | Crimps for female molex sockets | $0.12 | 100 | 0 | $0.00 | $12.20 | $12.20 | https://www.mouser.com/ProductDetail/538-43031-0007
Headers & Wire Housings FEMALE TERM 20-24 | 16 | Crimps for male molex sockets | $0.11 | 100 | 0 | $0.00 | $11.40 | $11.40 | https://www.mouser.com/ProductDetail/Molex/43030-0007?qs=MuwpYaHj75276x2HQaDYIw%3D%3D
Hook-up Wire 24AWG7/32 PTFE 100ft SPOOL WHT | 1 | PTFE wire stealhburner extenders | $89.54 | 1 | 0 | $0.00 | $89.54 | $89.54 | https://www.mouser.com/ProductDetail/602-5854-7-100-01
Educational Kits JST connector Kit (2.54mm) | 1 | JST connectors for trimming cables | $8.90 | 1 | 0 | $0.00 | $8.90 | $8.90 | https://www.mouser.com/ProductDetail/426-FIT0255
 |  |  |  |  |  | $0.00 | $137.70 | $137.70
Option 2: Canbus (Recommended) |  |  |  | Quantity |  |  | Remaining Subtotals
Description | Min Qty | Notes | Price | Desired | Ordered | Paid | Required | Overall | Link
Big Tree Tech EBB SB2209 | 1 | For Stealthburner | $39.99 | 1 | 0 | $0.00 | $39.99 | $39.99 | https://biqu.equipment/products/bigtreetech-ebb-sb2209-can-v1-0
U2C V2.1 | 0 | Can use RJ11 port on Octopus instead | $46.88 | 1 | 0 | $0.00 | $46.88 | $46.88 | https://biqu.equipment/products/bigtreetech-ebb-sb2209-can-v1-0?variant=40214284468322
30 PIN Wire + 100K NTC B3950 | 0 | Precrimped small wires (recommended) | $6.55 | 1 | 0 | $0.00 | $6.55 | $6.55 | https://biqu.equipment/products/bigtreetech-ebb-sb2209-can-v1-0?variant=40214285058146
25ft - 1/4 inch PET Expandable Braided Sleeving | 1 | Aesthetic covering for canbus wire | $8.99 | 1 | 0 | $0.00 | $8.99 | $8.99 | https://www.amazon.com/dp/B098NKKZ3B?psc=1&ref=ppx_yo2ov_dt_b_product_details
2PCS 1m 13# Steel Piano Music Wire | 1 | Pack of 2 | $5.99 | 1 | 0 | $0.00 | $5.99 | $5.99 | Amazon.com: Bstinay 2PCS 1m 13# Steel Piano Music Wire for Replacement of Broken Strings Dia 0.775mm Silver : Musical Instruments (https://www.amazon.com/Bstinay-Replacement-Broken-Strings-0-775mm/dp/B0C4NFLDRF)
Cable Connectors PG7 PG9 PG11 PG13.5 PG16 PG19 | 1 | PG7 is used | $12.99 | 1 | 0 | $0.00 | $12.99 | $12.99 | https://www.amazon.com/dp/B09Z26FF8B?ref=ppx_yo2ov_dt_b_product_details&th=1
 |  |  |  |  |  | $0.00 | $121.39 | $121.39
Panels
Buildplate

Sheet: 3_mods
3. Optional Modifications
1. Raspberry Pi 5
2. Dragon Burner V8 2.85mm Filament Toolhead
1. Raspberry Pi 5 |  |  |  | Quantity |  |  | Subtotals
Description | Min Qty | Notes | Price | Desired | Ordered | Paid | Expected | Remaining | Link
Raspberry Pi 5 (8 Gb) | 1 | Upgrade from included Raspberry Pi 4 | $80.00 | 1 | 0 | $0.00 | $80.00 | $80.00 | SC1112 Raspberry Pi | Mouser (https://www.mouser.com/ProductDetail/Raspberry-Pi/SC1112?qs=HoCaDK9Nz5c86n0i5EQ%2FPA%3D%3D)
Active Cooler | 1 | Necessary for Raspberry Pi 5 | $5.00 | 1 | 0 | $0.00 | $5.00 | $5.00 | SC1148 Raspberry Pi | Mouser (https://www.mouser.com/ProductDetail/Raspberry-Pi/SC1148?qs=HoCaDK9Nz5fqo0izK2taew%3D%3D)
BATIGE Micro HDMI Female & Type C 3.0 Female Flush Mount | 1 | Optional port access to Raspberry Pi | $15.99 | 1 | 0 | $0.00 | $15.99 | $15.99 | https://www.amazon.com/dp/B0C68HPHR2?psc=1&ref=ppx_yo2ov_dt_b_product_details
FFC / FPC Jumper Cables Raspberry Pi 5 FPC Cables - Display, 200mm | 1 | Display Cable for Raspberry Pi 5 | $1.00 | 1 | 0 | $0.00 | $1.00 | $1.00 | https://www.mouser.com/ProductDetail/358-SC1131
NVME Base for Raspberry Pi 5 | 1 | Allows for higher storage capacity | $14.36 | 1 | 0 | $0.00 | $14.36 | $14.36 | https://shop.pimoroni.com/products/nvme-base?variant=41219587178579
 |  |  |  |  |  | $0.00 | $116.35 | $116.35
2. Dragon Burner V8 2.85mm Filament Toolhead |  |  |  | Quantity |  |  | Subtotals
Description | Min Qty | Notes | Price | Desired | Ordered | Paid | Expected | Remaining | Link
Big Tree Tech EBB36 | 1 | Alternative canbus PCB | $29.99 | 1 | 0 | $0.00 | $29.99 | $29.99 | https://www.amazon.com/dp/B0CNXRZTKL?psc=1&ref=ppx_yo2ov_dt_b_product_details
22 AWG Black and Red Silicone Wire | 1 | Delivers power to PCB | $9.98 | 1 | 0 | $0.00 | $9.98 | $9.98 | https://www.amazon.com/gp/product/B077XBWX8V/ref=ppx_yo_dt_b_asin_title_o00_s00?ie=UTF8&psc=1
Ferrule Crimping Tool AWG 23-7 with 1900PCS Ferrules Kit | 1 | Crimping for hotend wiring | $23.98 | 1 | 0 | $0.00 | $23.98 | $23.98 | https://www.amazon.com/gp/product/B0CWP24SL5/ref=ppx_yo_dt_b_asin_title_o00_s00?ie=UTF8&psc=1
V6 All-Metal HotEnd | 1 | 2.85mm 24V Direct Drive | $45.39 | 1 | 0 | $0.00 | $45.39 | $45.39 | https://e3d-online.com/products/v6-all-metal-hotend?variant=40923457519675
40 x 40 x 10 mm Brushless Exhaust Cooler Printer Radiators | 2 | Side fans for cowl | $5.93 | 2 | 0 | $0.00 | $11.86 | $11.86 | https://www.aliexpress.us/item/2251832613009306.html
30 x 30 x 10 mm Dual Ball Bearing Brushless Car Lamp Cooling Fan | 1 | Pack of 2 | $8.54 | 1 | 0 | $0.00 | $8.54 | $8.54 | https://www.aliexpress.us/item/3256802670785330.html
Orbiter Extruder for 2.85/3.0MM Filament | 1 | Provided fully assembled | $56.90 | 1 | 0 | $0.00 | $56.90 | $56.90 | https://www.aliexpress.us/item/3256802594760158.html
Rainbow RGBW LEDs | 0 | Rainbow Barf | $5.88 | 1 | 0 | $0.00 | $5.88 | $5.88 | https://www.aliexpress.us/item/3256805225841575.html
FYSETC Sequins with RGB WS2812 3535 Bright RGB LED | 1 | Allows for higher storage capacity | $2.92 | 1 | 0 | $0.00 | $2.92 | $2.92 | https://www.aliexpress.us/item/3256805836898589.html
 |  |  |  |  |  | $0.00 | $195.44 | $195.44
Panels
Buildplate

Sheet: theme_white_orange
White and Orange Theme BOM
Note: Avoid using white ABS with Titanium Dioxide
Description | Min Qty | Notes | Price | Desired Qty | Ordered Qty | Remaining Subtotal | Link
White Drag Chain R18 10x11 Open | 2 | Replaces IGUS E2i-10-10-018-0 Chain | $7.24 | 2 | 0 | $14.48 | https://www.aliexpress.com/item/3256805618753942.html
White Drag Chain R28 10x15 Open | 2 | Replaces IGUS E2-15-10-028-0 Chain | $7.70 | 2 | 0 | $15.40 | https://www.aliexpress.com/item/3256805618753942.html
Orange Acrylic Sheet 36" x 24" x 1/8" (3mm) | 2 | Top and Base Panels (469x469x4 mm) | $24.95 | 2 | 0 | $49.90 | https://makerstock.com/products/orange-fluorescent-acrylic?variant=32575693357153
 |  | 24" x 24" x 1/8" would work here too
Orange Acrylic Sheet 24" x 48" x 1/8" (3mm) | 4 | Side and Back Panels (483x1103x4 mm) | $49.95 | 4 | 0 | $199.80 | https://makerstock.com/products/orange-fluorescent-acrylic?variant=40860284026977
 |  | Door Panels (241.5x1103x4 mm)
Natural PRO Series ABS Filament - 1.75mm (1kg) | 2 | For General Printed Parts (Whiteish Color) | $52.00 | 2 | 0 | $104.00 | https://www.matterhackers.com/store/l/pro-series-abs/sk/MGY429XU
Polymaker ABS Filament 1kg Orange | 1 | For Accented Printed Parts | $21.99 | 1 | 0 | $21.99 | https://www.amazon.com/dp/B09DKS7TFT?psc=1&ref=ppx_yo2ov_dt_b_product_details
Krylon I00500A07 12-Ounce Triple Thick Clear Glaze Aerosol Spray,High-Gloss (Pack of 2) | 2 | Protective coating over spray painted parts | $12.94 | 2 | 0 | $25.88 | https://www.amazon.com/Krylon-I00500A00-12-Ounce-Triple-Aerosol/dp/B0CFXJGNMV
Krylon K05545007 COLORmaxx Spray Paint and Primer for Indoor/Outdoor Use Gloss White 12 Oz | 8 | For Painting Extrusions, Fans, etc. | $6.04 | 8 | 0 | $48.32 | https://www.amazon.com/Krylon-K05545007-COLORmaxx-Spray-Aerosol/dp/B07LFWZ84M
 |  |  |  |  |  | $479.77
Panels
Buildplate

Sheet: reference_self_source
Self Source BOM (For Cost Comparison)
Build Volume (350mm x 350mm x 930mm)
Frame Dimensions (510mm x 510mm x 1130mm)
Category | Description | Min Qty | Notes | Custom | Price | Desired Qty | Ordered Qty | Base Subtotal | Custom Subtotal | Remaining Subtotal | Link
Fasteners | M5x40 SHCS | 22 |  | FALSE | $0.26 | 25 | 0 | $6.50 | $0.00 | $6.50 | https://www.boltdepot.com/Product-Details.aspx?product=6527
 | M5x30 BHCS | 22 |  | FALSE | $0.46 | 25 | 0 | $11.50 | $0.00 | $11.50 | https://www.boltdepot.com/Product-Details.aspx?product=15651
 | M5x16 BHCS | 35 |  | FALSE | $0.39 | 40 | 0 | $15.60 | $0.00 | $15.60 | https://www.boltdepot.com/Product-Details.aspx?product=15648
 | M5x10 BHCS | 35 |  | FALSE | $0.33 | 40 | 0 | $13.20 | $0.00 | $13.20 | https://www.boltdepot.com/Product-Details.aspx?product=15646
 | M5 Hexnut | 16 |  | FALSE | $0.06 | 30 | 0 | $1.80 | $0.00 | $1.80 | https://www.boltdepot.com/Product-Details.aspx?product=4785
 | M5 Post-install T-nut | 68 | 20-m5 100pcs | FALSE | $10.28 | 1 | 0 | $10.28 | $0.00 | $10.28 | https://www.aliexpress.us/item/2251832618848960.html?onelink_thrd=0.015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
 | M5 1mm Shim | 42 | Pack of 50 | FALSE | $8.62 | 1 | 0 | $8.62 | $0.00 | $8.62 | https://www.mcmaster.com/98055A099/
 | M4x6 BHCS | 7 |  | FALSE | $0.12 | 10 | 0 | $1.20 | $0.00 | $1.20 | https://www.boltdepot.com/Product-Details.aspx?product=18944
 | M4 Knurled Nut (DIN 466-B) | 4 |  | FALSE | $0.69 | 5 | 0 | $3.45 | $0.00 | $3.45 | https://www.aliexpress.us/item/3256803272722533.html?gatewayAdapt=glo2usa4itemAdapt
 | M3x40 SHCS | 30 |  | FALSE | $0.20 | 35 | 0 | $7.00 | $0.00 | $7.00 | https://www.boltdepot.com/Product-Details.aspx?product=6387
 | M3x30 SHCS | 25 |  | FALSE | $0.20 | 30 | 0 | $6.00 | $0.00 | $6.00 | https://www.boltdepot.com/Product-Details.aspx?product=13641
 | M3x20 SHCS | 22 |  | FALSE | $0.16 | 25 | 0 | $4.00 | $0.00 | $4.00 | https://www.boltdepot.com/Product-Details.aspx?product=13639
 | M3x16 SHCS | 20 |  | FALSE | $0.15 | 25 | 0 | $3.75 | $0.00 | $3.75 | https://www.boltdepot.com/Product-Details.aspx?product=13638
 | M3x12 SHCS | 41 |  | FALSE | $0.12 | 50 | 0 | $6.00 | $0.00 | $6.00 | https://www.boltdepot.com/Product-Details.aspx?product=13637
 | M3x10 FHCS | 4 |  | FALSE | $0.17 | 10 | 0 | $1.70 | $0.00 | $1.70 | https://www.boltdepot.com/Product-Details.aspx?product=13251
 | M3x6 FHCS | 8 |  | FALSE | $0.15 | 10 | 0 | $1.50 | $0.00 | $1.50 | https://www.boltdepot.com/Product-Details.aspx?product=13249
 | M3x8 SHCS | 247 |  | TRUE | $0.12 | 250 | 0 | $0.00 | $30.00 | $30.00 | https://www.boltdepot.com/Product-Details.aspx?product=13635
 | M3x6 BHCS | 11 |  | FALSE | $0.12 | 15 | 0 | $1.80 | $0.00 | $1.80 | https://www.boltdepot.com/Product-Details.aspx?product=13334
 | M3 Hexnut | 6 |  | FALSE | $0.06 | 10 | 0 | $0.60 | $0.00 | $0.60 | https://www.boltdepot.com/Product-Details.aspx?product=4783
 | M3 Post-install T-nut | 163 | 20-m3 100pcs | TRUE | $12.88 | 2 | 0 | $0.00 | $25.76 | $25.76 | https://www.aliexpress.us/item/2251832618848960.html?sk=KUHCwnu4&terminal_id=77b480c9601746d1be2247846d74a043
 | M3 Hammer Head T-nuts | 60 | 100 pieces | FALSE | $7.99 | 1 | 0 | $7.99 | $0.00 | $7.99 | https://www.amazon.com/dp/B07SDFCTD4/
 | M3 Washer | 3 |  | FALSE | $0.07 | 10 | 0 | $0.70 | $0.00 | $0.70 | https://www.boltdepot.com/Product-Details.aspx?product=4513
 | M3 Threaded Insert (M3x5x4) | 110 | 100 pieces | FALSE | $8.10 | 2 | 0 | $16.20 | $0.00 | $16.20 | https://www.aliexpress.us/item/2255800046543591.html
 | M2x10 Self-tapping Screw | 16 | 50 pieces | FALSE | $12.91 | 1 | 0 | $12.91 | $0.00 | $12.91 | https://www.mcmaster.com/99397A267/
Motion | GT2 80T Pulley (5mm ID 6mm W) | 4 | 4 pieces | FALSE | $32.99 | 1 | 0 | $32.99 | $0.00 | $32.99 | https://www.aliexpress.us/item/2251832596290407.html?gatewayAdapt=glo2usa4itemAdapt
 | GT2 20T Pulley (5mm ID 6mm W) | 3 | 3 pieces | FALSE | $8.99 | 1 | 0 | $8.99 | $0.00 | $8.99 | https://www.aliexpress.us/item/2251832539995194.html?gatewayAdapt=glo2usa4itemAdapt
 | GT2 20T Pulley (5mm ID 9mm W) | 4 | 5 pieces | FALSE | $15.99 | 1 | 0 | $15.99 | $0.00 | $15.99 | https://www.aliexpress.us/item/2251832464361177.html?gatewayAdapt=glo2usa4itemAdapt
 | GT2 16T Pulley (5mm ID 6mm W) | 4 | 5 pieces | FALSE | $9.99 | 1 | 0 | $9.99 | $0.00 | $9.99 | https://www.aliexpress.us/item/2251801558494240.html?gatewayAdapt=glo2usa4itemAdapt
 | GT2 20T Toothed Idler (5mm ID 6mm W) | 2 |  | FALSE | $1.99 | 2 | 0 | $3.98 | $0.00 | $3.98 | https://www.aliexpress.us/item/2251832539995194.html?gatewayAdapt=glo2usa4itemAdapt
 | GT2 20T Toothed Idler (5mm ID 9mm W) | 4 | 5 pieces | FALSE | $9.99 | 1 | 0 | $9.99 | $0.00 | $9.99 | https://www.aliexpress.us/item/2251832564177700.html?gatewayAdapt=glo2usa4itemAdapt
 | F695 Bearing | 20 | 10 pieces | FALSE | $4.19 | 2 | 0 | $8.38 | $0.00 | $8.38 | https://www.aliexpress.us/item/2251832814871526.html?gatewayAdapt=glo2usa4itemAdapt
 | 625 Bearing | 12 | 12 pieces | FALSE | $3.43 | 1 | 0 | $3.43 | $0.00 | $3.43 | https://www.aliexpress.us/item/2251832804890021.html?gatewayAdapt=glo2usa4itemAdapt
 | Ø5x60mm Shaft D Cut | 4 |  | FALSE | $0.99 | 4 | 0 | $3.96 | $0.00 | $3.96 | https://west3d.com/products/round-shafts-5x30mm-5x60mm?variant=41971073024212
 | Ø5x35mm Shaft (trim to size) | 1 |  | FALSE | $0.59 | 1 | 0 | $0.59 | $0.00 | $0.59 | https://west3d.com/products/round-shafts-5x30mm-5x60mm?variant=41971073024212
 | GT2 Belt Loop (6mm W) - 188mm | 4 | 5 pieces | FALSE | $4.99 | 1 | 0 | $4.99 | $0.00 | $4.99 | https://www.aliexpress.us/item/2255799847707082.html?gatewayAdapt=glo2usa4itemAdapt
 | GT2 Open Belt LL-2GT-9 (9mm wide) - 2400mm | 4 | Length 3M | TRUE | $13.80 | 5 | 0 | $0.00 | $69.00 | $69.00 | https://www.aliexpress.us/item/2251832667244886.html?gatewayAdapt=glo2usa4itemAdapt
 | BMG Extruder Components Kit | 1 |  | FALSE | $15.25 | 1 | 0 | $15.25 | $0.00 | $15.25 | https://www.aliexpress.us/item/2255799834871688.html
 | Linear Rail MGN9H 400mm | 2 | GS_MGN9-1H-B400 | FALSE | $15 | 2 | 0 | $30.00 | $0.00 | $30.00 | https://www.robotdigg.com/product/1314/Black-anodized-linear-rail-7,-9,-12-and-15
 | Linear Rail MGN9H 1000mm | 4 |  | TRUE | $66 | 4 | 0 | $0.00 | $264.00 | $264.00 | https://3dprintingusa.com/products/9mm-linear-rail-1000mm-with-one-mgn9h-block
 | Linear Rail MGN12H 400mm | 1 | GS_MGN12-1H-B400 | FALSE | $15 | 1 | 0 | $15.00 | $0.00 | $15.00 | https://www.robotdigg.com/product/1314/Black-anodized-linear-rail-7,-9,-12-and-15
 | GT2 Open Belt LL-2GT-6 (6mm wide) - 2000mm | 2 | Length 2M | FALSE | $6.20 | 3 | 0 | $18.60 | $0.00 | $18.60 | https://www.aliexpress.us/item/2251832667244886.html?gatewayAdapt=glo2usa4itemAdapt
Electronics | Omron D2F-01L Micro Switch | 3 |  | FALSE | $2.02 | 4 | 0 | $8.08 | $0.00 | $8.08 | https://www.digikey.com/en/products/detail/omron-electronics-inc-emc-div/D2F-01L/83264
 | Inductive Probe (See sourcing guide) | 1 |  | FALSE | $7.00 | 1 | 0 | $7.00 | $0.00 | $7.00 | https://www.aliexpress.us/item/2251832663198775.html?gatewayAdapt=glo2usa
 | Hotend Kit (24V) | 1 |  | FALSE |  |  | 0 | $0.00 | $0.00 | $0.00
 | 40x40x20 Centrifugal Fan (24V) | 1 | 2 pieces | FALSE | $23.64 | 1 | 0 | $23.64 | $0.00 | $23.64 | https://www.aliexpress.us/item/3256801278415934.html?gatewayAdapt=glo2usa4itemAdapt
 | 40x40x10 Axial Fan (24V) | 1 |  | FALSE | $16.12 | 1 | 0 | $16.12 | $0.00 | $16.12 | https://www.aliexpress.us/item/2251832540325686.html?gatewayAdapt=glo2usa4itemAdapt
 | Mini 12864 Display | 1 | Possibly Optional | FALSE | $13.42 | 1 | 0 | $13.42 | $0.00 | $13.42 | https://www.amazon.com/BIGTREETECH-Mini12864-Graphic-Display-Prusa-i3/dp/B08P5LXR86
 | ZF Rocker Switch DPST 16A ON-OFF | 1 |  | FALSE | $3.00 | 1 | 0 | $3.00 | $0.00 | $3.00 | https://www.mouser.com/ProductDetail/ZF/WRG32F2BBRLN
 | ↱ TycoElectronics 10EGG1-1 Filtered Power Inlet (NA/UK) | 1 | Single Fuse | FALSE | $20.40 | 1 | 0 | $20.40 | $0.00 | $20.40 | https://www.mouser.com/ProductDetail/TE-Connectivity-PB/10EGG1-1?qs=vcjNRp8H9z1CsIf%2F5OknUw%3D%3D
 | ↳ TycoElectronics 10EGG1-2 Filtered Power Inlet (EU) | 1 | Dual Fuse | FALSE | $21.43 | 0 | 0 | $0.00 | $0.00 | $0.00 | https://www.mouser.com/ProductDetail/TE-Connectivity-PB/10EGG1-2/?qs=vcjNRp8H9z2nhEkRL4AXYw%3D%3D
 | ↱ Medium Blow Fuse 5x20mm 4A (220V mains) | 2 | Europe | FALSE | $1.11 | 0 | 0 | $0.00 | $0.00 | $0.00 | https://www.digikey.com/en/products/detail/littelfuse-inc/0232004-MXP/778023
 | ↳ Medium Blow Fuse 5x20mm 8A (120v mains) | 2 | North America | FALSE | $1.11 | 2 | 0 | $2.22 | $0.00 | $2.22 | https://www.digikey.com/en/products/detail/littelfuse-inc/0232008-MXP/778029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
 | Keystone CAT6 Insert (Optional) | 1 | Include Tool | FALSE | $75.95 | 0 | 0 | $0.00 | $0.00 | $0.00 | https://www.amazon.com/EMS-easyJACK-CAT6A-Kit-Termination/dp/B09S17YX4T
 | 60x60x20 Fan (24V) | 3 | 3 pieces | FALSE | $18.00 | 1 | 0 | $18.00 | $0.00 | $18.00 | https://www.amazon.com/dp/B08577444D
 | Controller with 7+ Stepper outputs | 1 | BTT Octopus V1.1 | FALSE | $55.99 | 1 | 0 | $55.99 | $0.00 | $55.99 | https://www.amazon.com/BIGTREETECH-Direct-Octopus-Control-Supports/dp/B094Y77FQN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
 | ↳ USB Cable for selected controller | 1 | Included above | FALSE | $12.99 | 0 | 0 | $0.00 | $0.00 | $0.00 | https://www.amazon.com/SUNGUY-Android-Charging-Compatible-External/dp/B0B28ZCV2Y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
 | TMC2209 Stepper Motor Driver | 7 | 6 Pieces | FALSE | $29.99 | 2 | 0 | $59.98 | $0.00 | $59.98 | https://www.amazon.com/BIGTREETECH-Direct-TMC2209-Stepper-Control/dp/B08WZFK9KT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
 | RaspberryPi 3B+ or better | 1 | RaspberryPi 5 8GB | FALSE | $80.00 | 1 | 1 | $80.00 | $0.00 | $0.00 | https://www.mouser.com/ProductDetail/Raspberry-Pi/SC1112?qs=HoCaDK9Nz5c86n0i5EQ%2FPA%3D%3D
 | Mean Well LRS-200-24 PSU | 1 |  | FALSE | $31.63 | 1 | 0 | $31.63 | $0.00 | $31.63 | https://www.digikey.com/en/products/detail/mean-well-usa-inc/LRS-200-24/7705026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
 | Mean Well RS-25-5 PSU | 1 |  | FALSE | $12.73 | 1 | 0 | $12.73 | $0.00 | $12.73 | https://www.digikey.com/en/products/detail/mean-well-usa-inc/RS-25-5/7706180
 | Omron G3A-210B-DC5 SSR | 1 |  | FALSE | $32.66 | 1 | 0 | $32.66 | $0.00 | $32.66 | https://www.digikey.com/en/products/detail/omron-automation-and-safety/G3NA-210B-UTU-DC5-24/634443?
 | DIN Rail Mount Bracket for G3A SSR | 1 |  | FALSE | $9.90 | 1 | 0 | $9.90 | $0.00 | $9.90 | https://www.digikey.com/en/products/detail/idec/BAA1000/8344276
 | BAT85 Diode | 1 |  | FALSE | $0.26 | 10 | 0 | $2.55 | $0.00 | $2.55 | https://www.digikey.com/en/products/detail/BAT85S-TR/BAT85SCT-ND/3104371
 | C13 Power Cord | 1 |  | FALSE | $9.99 | 1 | 1 | $9.99 | $0.00 | $0.00 | https://www.amazon.com/StarTech-com-Computer-Replacement-Monitor-Printer/dp/B07D5RQBJQ
 | Thermal Fuse (125C) | 1 | 5 pieces | FALSE | $3.00 | 1 | 0 | $3.00 | $0.00 | $3.00 | https://www.aliexpress.us/item/2251832699177528.html?gatewayAdapt=glo2usa4itemAdapt
 | NEMA17 Motor 17HS19-2004S | 6 | 6 + 1 Pack | FALSE | $80.39 | 1 | 0 | $80.39 | $0.00 | $80.39 | https://www.omc-stepperonline.com/voron-2-4-afterburner-3d-printer-upgraded-nema-17-stepper-motor-kit-17hs19-2004s1-h-17hs08-1004s-h-voron24
 | ↳ NEMA17 Motor 17HS08-1004S | 1 | Included above | FALSE |  | 0 | 0 | $0.00 | $0.00 | $0.00 | https://www.omc-stepperonline.com/voron-2-4-afterburner-3d-printer-upgraded-nema-17-stepper-motor-kit-17hs19-2004s1-h-17hs08-1004s-h-voron24
Vibration Management | Rubber Foot (1.5x.75", 38x19mm) | 4 | 4 pieces | FALSE | $11.49 | 1 | 0 | $11.49 | $0.00 | $11.49 | https://www.amazon.com/uxcell-47mmx18mm-Compressor-Replacement-Black/dp/B0711Y6T56
Frame | OpenBuilds Billet Angle Corner Connector (2020) | 4 |  | FALSE | $2.99 | 4 | 0 | $11.96 | $0.00 | $11.96 | https://openbuildspartstore.com/black-angle-corner-connector/
 | Misumi HFSB5-2020-340 | 1 |  | FALSE | $5.16 | 1 | 0 | $5.16 | $0.00 | $5.16 | https://us.misumi-ec.com/vona2/detail/110302683830/?Inch=0&Tab=wysiwyg_area_0
 | DIN 3 Rails (35mm W) - 465mm | 2 | Find better fit | FALSE | $9.90 | 2 | 0 | $19.80 | $0.00 | $19.80 | https://www.digikey.com/en/products/detail/idec/BAA1000/8344276
 | Misumi HFSB5-2020-430 | 1 |  | FALSE | $6.53 | 1 | 0 | $6.53 | $0.00 | $6.53 | https://us.misumi-ec.com/vona2/detail/110302683830/?Inch=0&Tab=wysiwyg_area_0
 | Misumi HFSB5-2020-450 | 2 |  | FALSE | $6.84 | 2 | 0 | $13.68 | $0.00 | $13.68 | https://us.misumi-ec.com/vona2/detail/110302683830/?Inch=0&Tab=wysiwyg_area_0
 | Misumi HFSB5-2020-470-TPW | 10 |  | FALSE | $7.14 | 10 | 0 | $71.40 | $0.00 | $71.40 | https://us.misumi-ec.com/vona2/detail/110302683830/?Inch=0&Tab=wysiwyg_area_0
 | Misumi HFSB5-2020-1130-LCP-RCP | 4 |  | TRUE | $25.97 | 4 | 0 | $0.00 | $103.88 | $103.88 | https://us.misumi-ec.com/vona2/detail/110302683830/?Inch=0&Tab=preview
Misc | Fume Extractor Carbon Filter Element | 1 | 6 Pack | FALSE | $12.99 | 1 | 0 | $12.99 | $0.00 | $12.99 | https://www.amazon.com/Extractor-Replacement-Activated-Absorber-Xytronic/dp/B07D5SBPN8?s=industrial
 | 4mm Threaded Bowden Coupler | 1 |  | FALSE | $10.04 | 1 | 0 | $10.04 | $0.00 | $10.04 | https://www.aliexpress.us/item/3256801221826511.html?gatewayAdapt=glo2usa4itemAdapt
 | 3M VHB Tape 5952 | 1 |  | FALSE | $3.14 | 1 | 0 | $3.14 | $0.00 | $3.14 | https://www.aliexpress.us/item/2251832698701344.html?gatewayAdapt=glo2usa4itemAdapt
 | Loctite Blue Threadlocker | 1 |  | FALSE | $7.87 | 1 | 0 | $7.87 | $0.00 | $7.87 | https://www.amazon.com/Loctite-Heavy-Duty-Threadlocker-Single/dp/B000I1RSNS
 | Mobil EP1/2 Grease | 1 |  | FALSE | $12.61 | 0 | 0 | $0.00 | $0.00 | $0.00 | https://www.amazon.com/Mobilux-Grease-NLGI-13-7-oz/dp/B01N191WZE?s=industrial
 | Single Sided Foam Tape 1mm Thick (5m) | 1 | 10 meters | FALSE | $3.14 | 2 | 0 | $6.28 | $0.00 | $6.28 | https://www.aliexpress.us/item/2251832698701344.html?gatewayAdapt=glo2usa4itemAdapt
 | Single Sided Foam Tape 3mm Thick (5m) | 1 |  | FALSE |  |  | 0 | $0.00 | $0.00 | $0.00
 | Ø6x3mm Neodimium Magnet | 8 |  | FALSE |  |  | 0 | $0.00 | $0.00 | $0.00
 | PTFE Tube (4mm OD 3mm ID) - 1000mm | 1 | 9.84 ft | TRUE | $7.99 | 1 | 0 | $0.00 | $7.99 | $7.99 | https://www.amazon.com/uxcell-Temperature-Multifunctional-Insulating-Transparent/dp/B0915QTF1G?s=industrial
 | PTFE Tube (4mm OD 2mm ID) - 300mm | 1 | 9.84 ft | TRUE | $8.99 | 1 | 0 | $0.00 | $8.99 | $8.99 | https://www.amazon.com/uxcell-Temperature-Multifunctional-Insulating-Transparent/dp/B0915BM1JD?s=industrial
Cables | Nylon Cable Ties Small (.07-.10", 1.8-2.7mm wide) | 42 | 1000 pieces | FALSE | $11.99 | 1 | 0 | $11.99 | $0.00 | $11.99 | https://www.amazon.com/gp/product/B01M06HTVH/
 | 18AWG Wire (10ft/3m total) | 1 |  | FALSE | $15.99 | 1 | 0 | $15.99 | $0.00 | $15.99 | https://www.amazon.com/gp/product/B01LH1G2IE/?th=1
 | 20AWG High-flex Wire (10ft/3m total) | 1 | 20 AWG 6 colors 23ft | FALSE | $15.49 | 1 | 0 | $15.49 | $0.00 | $15.49 | https://www.amazon.com/Electronics-different-Insulated-Temperature-Resistance/dp/B07G2GLKMP
 | 22-24AWG High-flex Wire (min 19 strand)(250ft/76m total) | 1 | 24 AWG 5 colors | FALSE | $15.99 | 1 | 0 | $15.99 | $0.00 | $15.99 | https://www.amazon.com/StrivedayTMFlexible-Silicone-Electric-electronic-electrics/dp/B01LH1G2IE?th=1
 | Female Spade Crimp Terminal (18-22AWG, 0.25" 6.35mm) | 7 |  | FALSE |  |  | 0 | $0.00 | $0.00 | $0.00
 | Fork Spade Crimp Terminal (18-22AWG #10) | 5 |  | FALSE |  |  | 0 | $0.00 | $0.00 | $0.00
 | Ring Crimp Terminal (16-22AWG #6) | 1 |  | FALSE |  |  | 0 | $0.00 | $0.00 | $0.00
 | JST XH Connector 3 Position Male / Femail Pair plus Pins | 1 |  | FALSE |  |  | 0 | $0.00 | $0.00 | $0.00
 | Connector kit matching your controller choice (usually JST-XH) | 1 |  | FALSE |  |  | 0 | $0.00 | $0.00 | $0.00
 | Crimp Ferrule Kit (covering sizes 24AWG to 18AWG) | 1 |  | FALSE |  |  | 0 | $0.00 | $0.00 | $0.00
 | 24 AWG PTFE (100ft Spool) | 1 | Toolhead wiring | TRUE | $89.54 | 1 | 0 | $0.00 | $89.54 | $89.54 | https://www.mouser.com/ProductDetail/602-5854-7-100-01
 | MicroFit3 Female Pin | 28 | For 20 - 24 AWG | TRUE | $0.08 | 100 | 0 | $0.00 | $8.30 | $8.30 | https://www.mouser.com/ProductDetail/538-43030-0001-CT
 | MicroFit3 Connector Plug 14 Position | 2 | LDO toolhead plug | TRUE | $1.02 | 2 | 0 | $0.00 | $2.04 | $2.04 | https://www.mouser.com/ProductDetail/538-43025-1410
 | MicroFit3 Connector Plug 4 Position | 4 |  | FALSE | $0.44 | 5 | 0 | $2.20 | $0.00 | $2.20 | https://www.digikey.com/en/products/detail/molex/0436400401/268986?s=N4IgTCBcDaICwGYBscAMBaVaCMIC6AvkA
 | MicroFit3 Connector Plug 3 Position | 1 |  | FALSE | $0.47 | 2 | 0 | $0.94 | $0.00 | $0.94 | https://www.digikey.com/en/products/detail/molex/0436400301/268985?s=N4IgTCBcDaICwGYBscAMBaVDUEYQF0BfIA
 | MicroFit3 Connector Plug 2 Position | 2 |  | FALSE | $0.42 | 6 | 0 | $2.52 | $0.00 | $2.52 | https://www.digikey.com/en/products/detail/molex/0436400201/268984?s=N4IgTCBcDaICwGYBscAMBaVZUEYQF0BfIA
 | MicroFit3 Connector Receptacle 4 Position | 4 |  | FALSE | $0.48 | 5 | 0 | $2.40 | $0.00 | $2.40 | https://www.digikey.com/en/products/detail/molex/0436450400/268976?s=N4IgTCBcDaICwGYBscCsBaADHTmQF0BfIA
 | MicroFit3 Connector Receptacle 3 Position | 1 |  | FALSE | $0.47 | 2 | 0 | $0.94 | $0.00 | $0.94 | https://www.digikey.com/en/products/detail/molex/0436450300/268975?s=N4IgTCBcDaICwGYBscCsBaADAzmQF0BfIA
 | MicroFit3 Connector Receptacle 2 Position | 2 |  | FALSE | $0.40 | 6 | 0 | $2.40 | $0.00 | $2.40 | https://www.digikey.com/en/products/detail/molex/0436450200/268974?s=N4IgTCBcDaICwGYBscCsBaADGTmQF0BfIA
 | MLX Power Receptacle 3 Position (bed wiring) | 1 |  | FALSE | $0.62 | 2 | 0 | $1.24 | $0.00 | $1.24 | https://www.digikey.com/en/products/detail/molex/0050842030/134562?s=N4IgTCBcDaIKwAYC0AOALEsCDMCQF0BfIA
 | MLX Power Plug 3 Position | 1 |  | FALSE | $0.35 | 2 | 0 | $0.70 | $0.00 | $0.70 | https://www.digikey.com/en/products/detail/molex/0050841030/63492?s=N4IgTCBcDaIKwAYC0AOALEgjAgzAkAugL5A
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

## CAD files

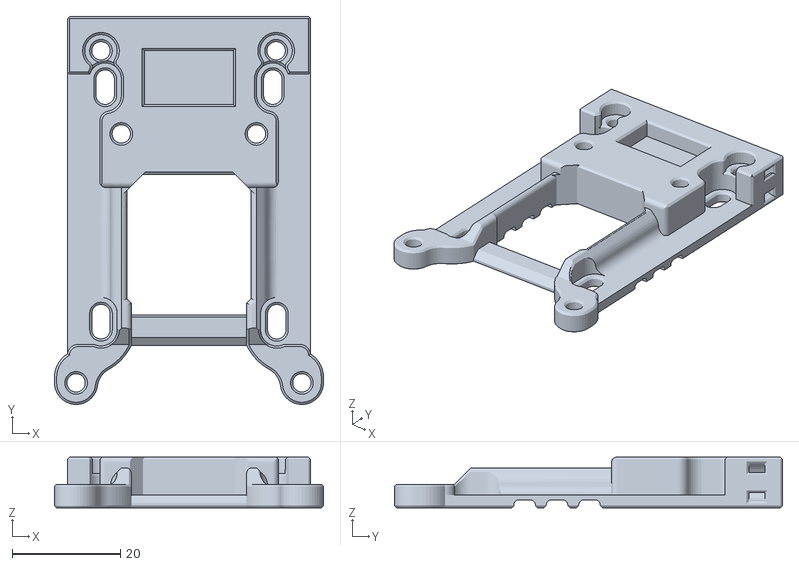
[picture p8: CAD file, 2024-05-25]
Printed_Parts/STLs/Toolheads/Dragon_Burner/Tap/Tap_Main_Spacer.stl
49.8 x 71.8 x 9.40

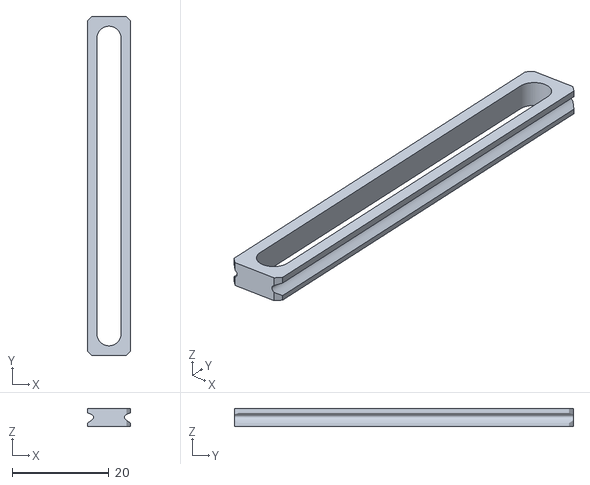
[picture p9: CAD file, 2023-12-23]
STLs/Mods/Voron_Tap/MGN9_Assembly_Tool.stl
8.90 x 70.0 x 3.80

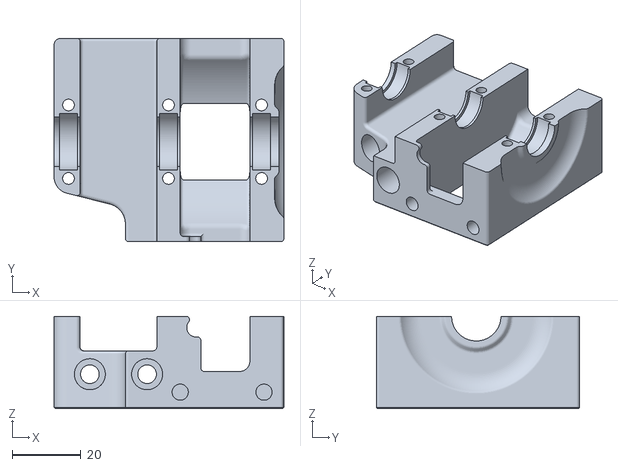
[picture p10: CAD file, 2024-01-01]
Printed_Parts/STLs/Z_Drive/z_drive_main_b_x2.stl
66.7 x 59.0 x 26.8

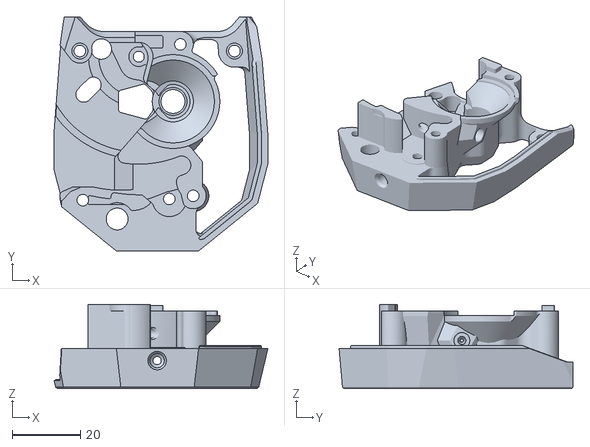
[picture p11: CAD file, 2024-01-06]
Printed_Parts/STLs/Toolheads/Voron_Stealthburner/Clockwork2/Direct_Drive/main_body.stl
62.8 x 68.7 x 24.7

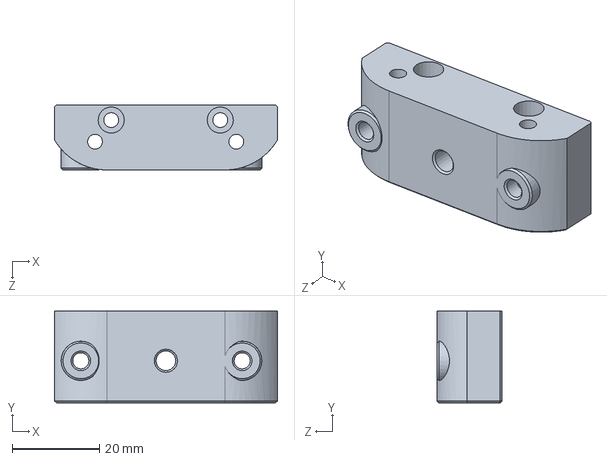
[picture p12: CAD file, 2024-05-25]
CAD/Orbiter2_Extruder_Mount_2.85.SLDPRT
51.1 x 21.0 x 14.9 mm

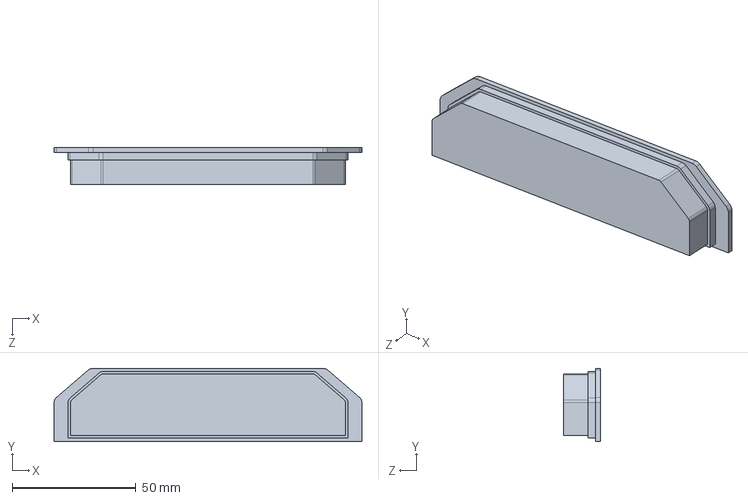
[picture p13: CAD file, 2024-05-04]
CAD/Panels/Handle_Cover.SLDPRT
124.6 x 29.7 x 15.0 mm

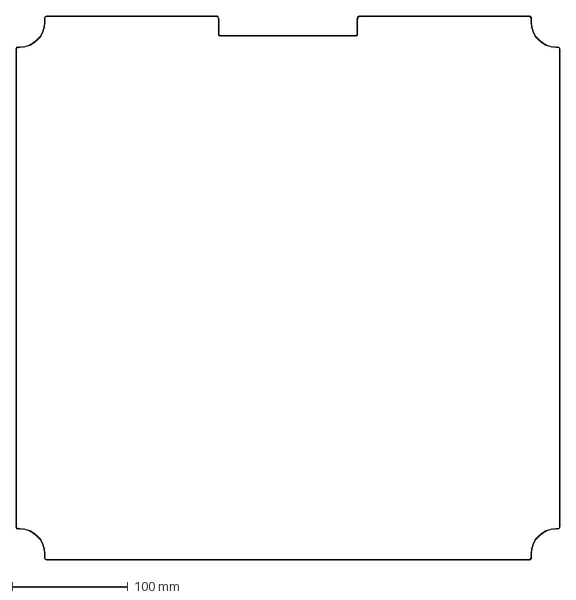
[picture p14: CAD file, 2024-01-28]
Drawing_DXFs/Panels/Bottom_Panel.dxf
469.2 x 469.2 mm

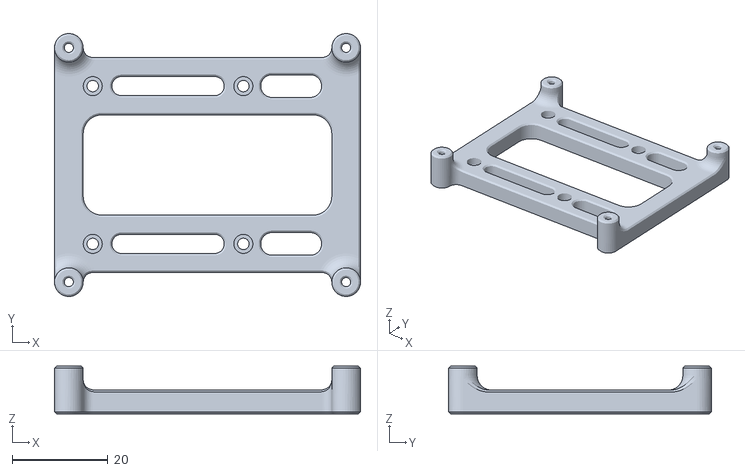
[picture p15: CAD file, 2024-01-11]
Printed_Parts/STLs/Electronics_Bay/LDO_beefy_raspberry_bracket.stl
64.0 x 55.0 x 10.0

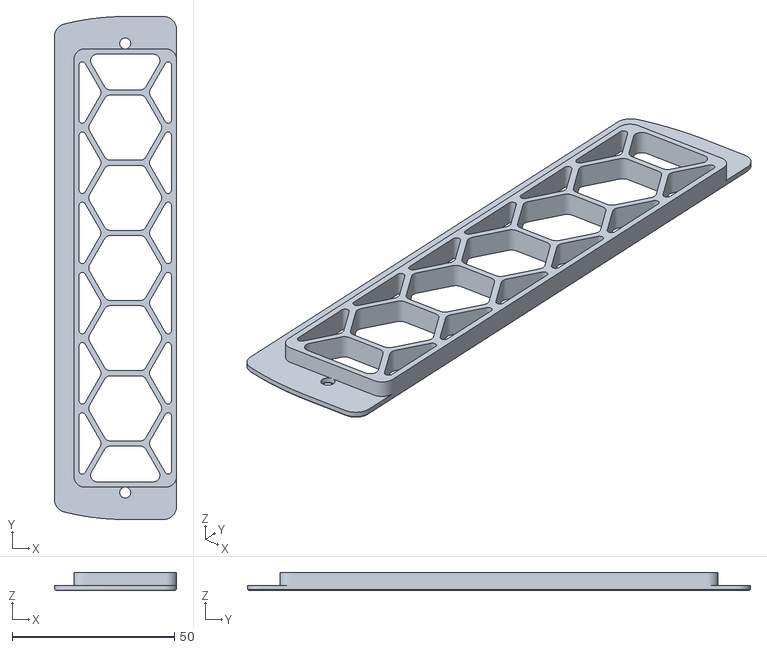
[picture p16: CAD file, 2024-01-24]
Printed_Parts/STLs/Exhaust_Filter/exhaust_filter_grill.stl
37.6 x 154.8 x 5.60

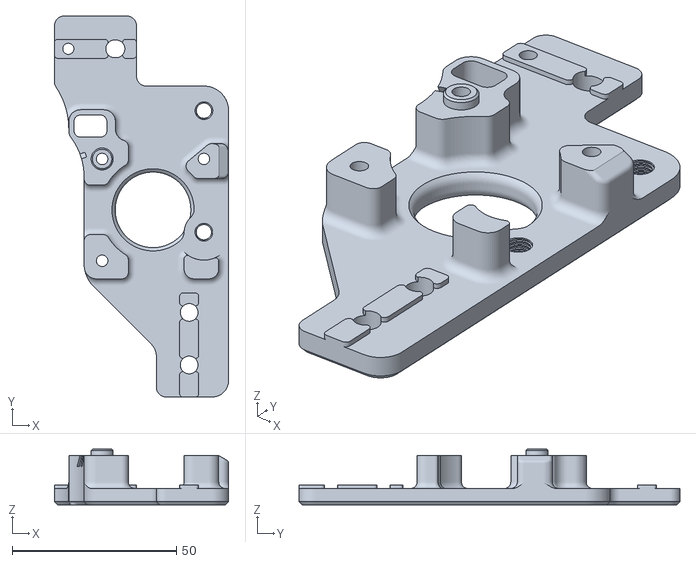
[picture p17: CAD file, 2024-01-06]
Printed_Parts/STLs/Gantry/AB_Drive_Units/b_drive_frame_lower.stl
53.0 x 116.0 x 17.0

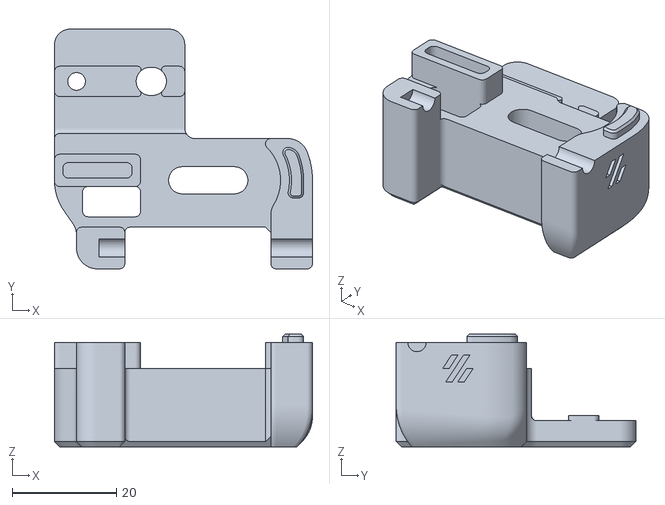
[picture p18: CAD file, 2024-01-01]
Printed_Parts/STLs/Gantry/Front_Idlers/front_idler_right_lower.stl
49.5 x 46.0 x 21.6

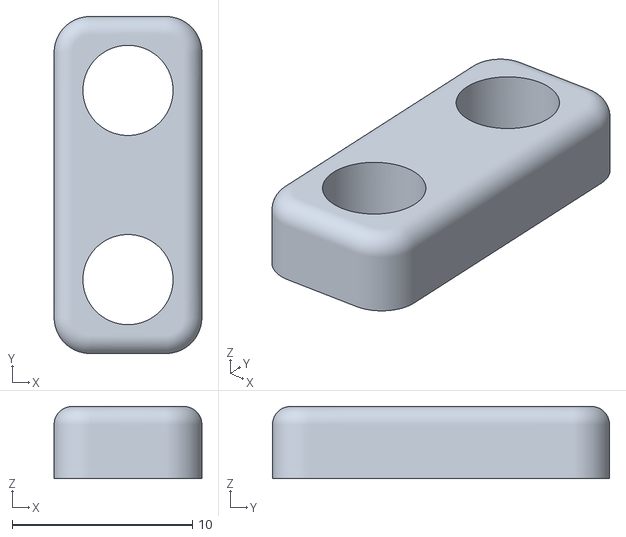
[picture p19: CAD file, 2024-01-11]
Printed_Parts/STLs/Gantry/X_Axis/X_Carriage/probe_retainer_bracket.stl
8.20 x 18.7 x 4.00

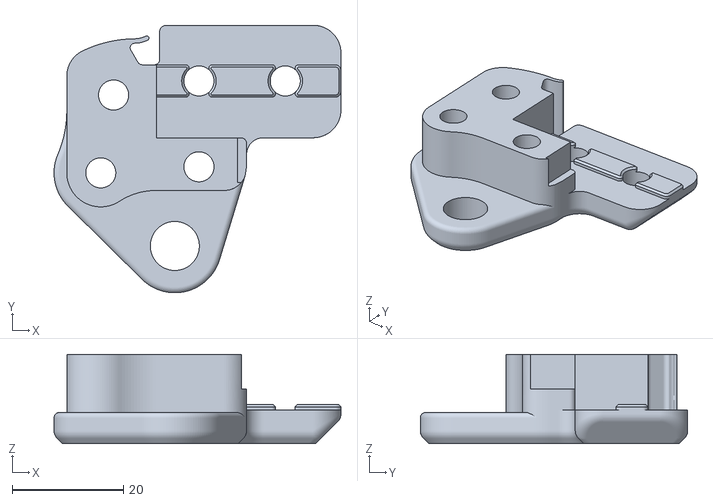
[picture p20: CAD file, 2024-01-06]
Printed_Parts/STLs/Gantry/X_Axis/XY_Joints/xy_joint_right_upper_MGN12.stl
51.5 x 48.0 x 16.0

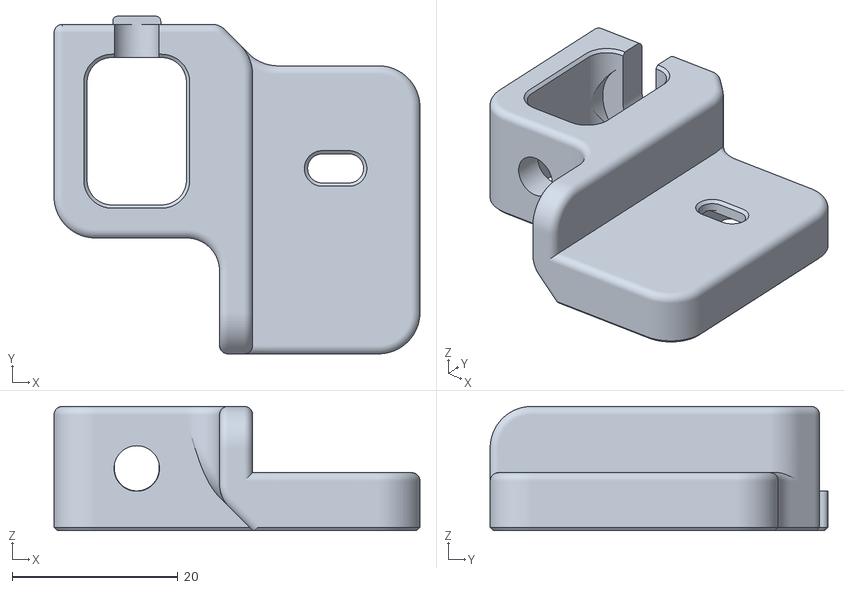
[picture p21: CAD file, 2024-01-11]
Printed_Parts/STLs/Gantry/z_chain_bottom_anchor.stl
44.2 x 40.8 x 15.0

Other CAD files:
Printed_Parts/STLs/Z_Drive/z_drive_main_a_x2.stl
Printed_Parts/STLs/Gantry/Z_Joints/z_joint_upper_x4.stl
Printed_Parts/STLs/Mods/Cable_Port_Flush_Mount_Skirt/rear_center_skirt_350.STL
Printed_Parts/STLs/Mods/Enclosed_Z_Chain_Guide/Enclosed_Z_Chain_Guide_With_Logo.STL
CAD/Orbiter2_Extruder_Mount_2.85mm.SLDPRT
CAD/Panels/Back_Panel.SLDPRT
CAD/Panels/Door_Panel.SLDPRT
CAD/Panels/Side_Panel.SLDPRT
CAD/Panels/Side_Panel_With_Handle.SLDPRT
CAD/Panels/Top_Panel.SLDPRT
Drawing_DXFs/Panels/Back_Panel.DXF
Drawing_DXFs/Panels/Deck_Panel.dxf
Drawing_DXFs/Panels/Door_Panel.DXF
Drawing_DXFs/Panels/Side_Panel.DXF
Drawing_DXFs/Panels/Side_Panel_With_Handle.DXF
Drawing_DXFs/Panels/Top_Panel.DXF
Printed_Parts/STLs/Electronics_Bay/LDO_bed_wago_mount.stl
Printed_Parts/STLs/Electronics_Bay/LED_Bar_Clip_Misumi_version2_x24.stl
Printed_Parts/STLs/Electronics_Bay/Octopus_bracket_set.stl
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

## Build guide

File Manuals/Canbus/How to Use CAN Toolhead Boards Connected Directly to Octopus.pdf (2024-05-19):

How to Use CAN Toolhead Boards Connected Directly to Octopus / Octopus Pro on CanBoot

- Klipper has a new CAN bus feature, the USB to CAN bus bridge communication for Octopus boards (and other compatible MCUs).
- This feature allows the Octopus boards (and other compatible MCUs) to act as a USB to CAN bus adapter. This replaces the need for an adapter like a Raspberry Pi CAN HAT, canable adapter, or the Bigtreetech U2C board.

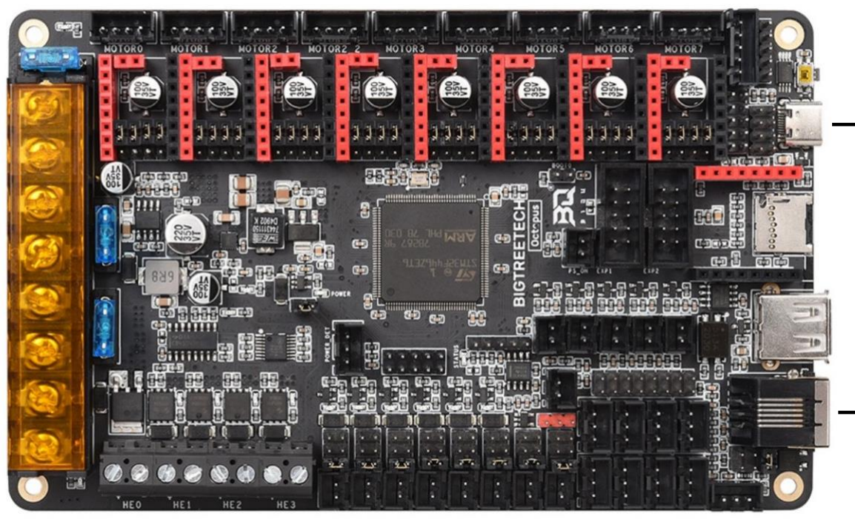
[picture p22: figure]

What is CanBoot?

- CanBoot is a custom bootloader loaded onto your Octopus and EBB board that allows users to update Klipper firmware over USB, UART, or CAN comms without physically having to access the board reset buttons or BOOT jumpers.
- It uses the same ‘make menuconfig’ setup to configure and compile firmware.
- CanBoot is NOT required to use the Klipper USB to CAN bus bridge comms. But I have not tested this comms feature separately.

You Will Need the Following

- USB-A to USB-C cable
- Power supply for Octopus and EBB toolboard (i.e. printer)
- RJ11 or RJ12 telephone cable, crimped to connect EBB board to Octopus
- See wiring info at end of guide. Best to setup wiring before installing software.
- Raspberry Pi, or similar, with Klipper / Moonraker / UI installed and working
- Computer with following software:
- SSH terminal software, I use PuTTY or Windows CMD
- WinSCP, to transfer files between Raspberry Pi and computer
- I also use Windows CMD to do this
- STM32CubeProgrammer
- Download for your computer OS and install
- https://www.st.com/en/development-tools/stm32cubeprog.html#get-software (https://www.st.com/en/development-tools/stm32cubeprog.html%23get-software)

High Level Instructions, for Understanding

1. Install CanBoot on Raspberry Pi, flash firmware to boards
a. Configure and compile CanBoot firmware for Octopus / Pro and EBB
b. Flash CanBoot to boards using STM32CubeProgrammer and computer
2. Setup boards for Klipper
a. Octopus - Setup Klipper for USB to CAN bus bridge, with CAN comms to EBB
b. EBB - Setup Klipper for CAN comms
c. Find serial device for Octopus / Pro on Raspberry Pi
d. Flash Klipper to Octopus / Pro with CanBoot serial command
3. Setup can0 network on Raspberry Pi, power cycle printer
4. Find CAN uuid for Boards
a. Connect EBB to Octopus / Pro, power cycle printer
5. Flash Klipper to EBB board with CanBoot CAN command
6. Printer Config Update and General Tips
7. How to Use CanBoot to update boards, Tips

Okay, enough talking! Let’s get started!

Instructions________________________________________________________________________

1. Install CanBoot on Raspberry Pi, flash firmware to boards

Start your SSH terminal.

sudo apt-get install git -y #Do this if you haven’t installed git yet…

git clone https://github.com/Arksine/CanBoot

cd CanBoot

make menuconfig

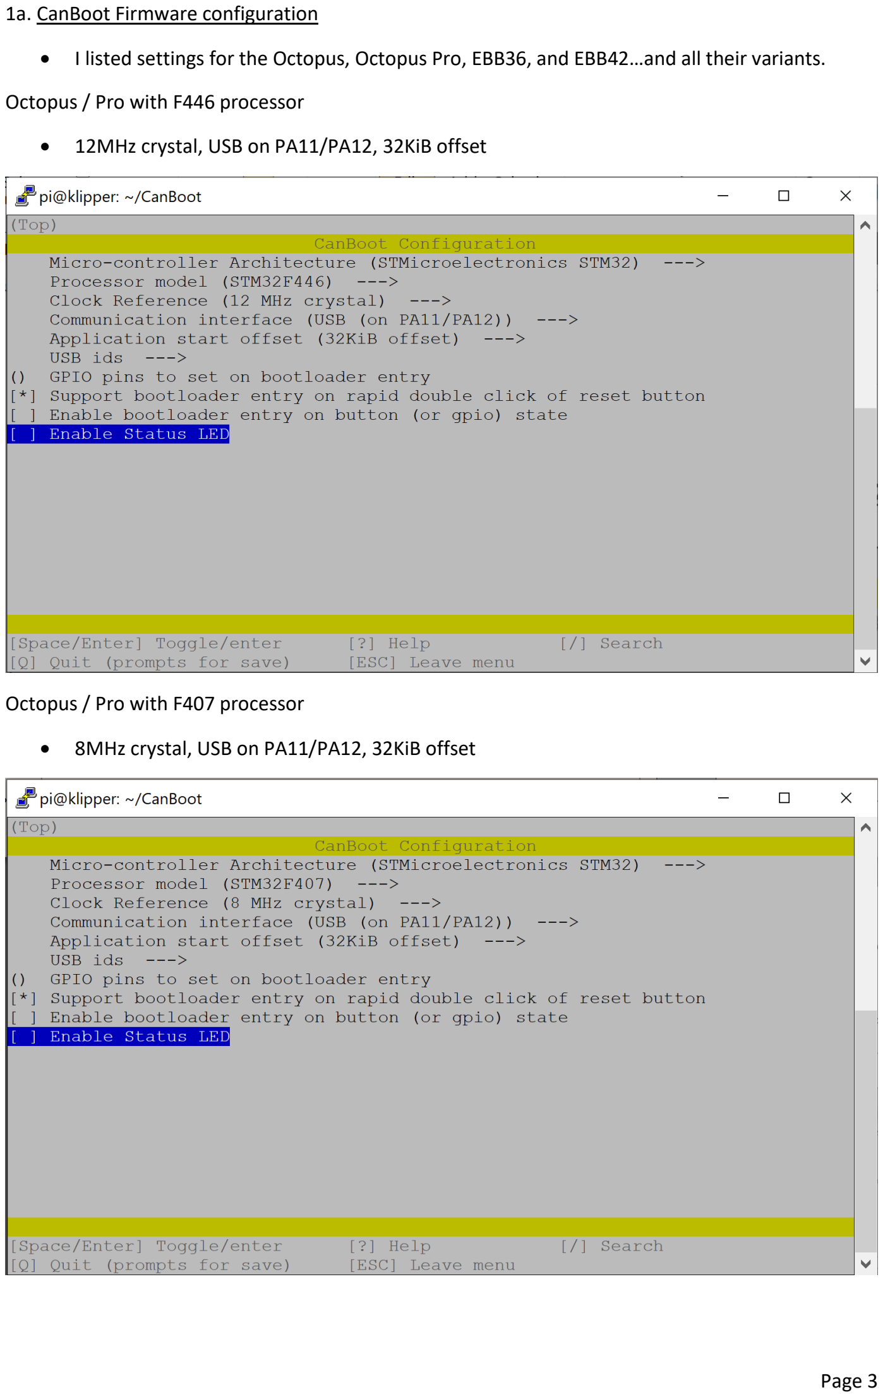
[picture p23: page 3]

1a. CanBoot Firmware configuration

- I listed settings for the Octopus, Octopus Pro, EBB36, and EBB42…and all their variants.

Octopus / Pro with F446 processor

- 12MHz crystal, USB on PA11/PA12, 32KiB offset

Octopus / Pro with F407 processor

- 8MHz crystal, USB on PA11/PA12, 32KiB offset

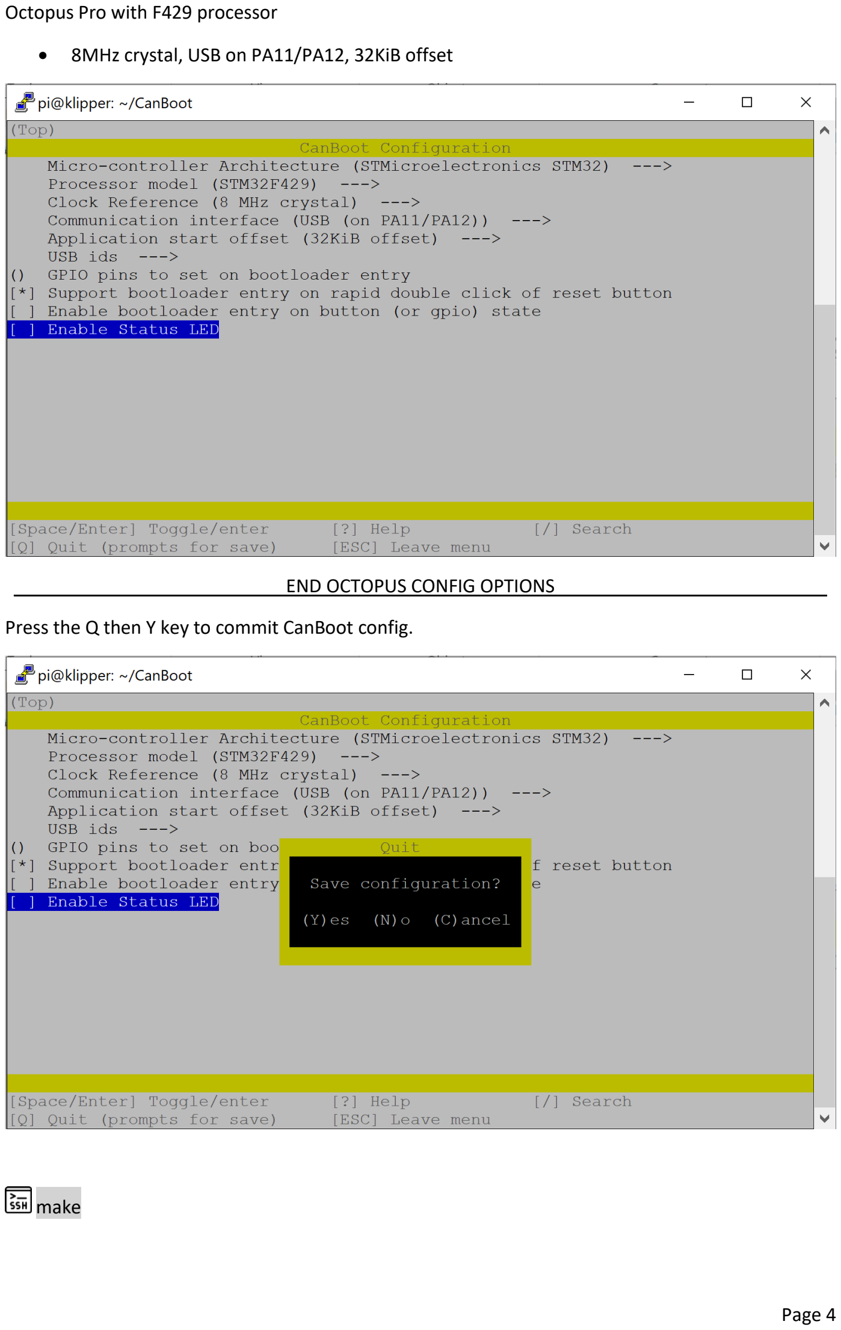
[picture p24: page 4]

Octopus Pro with F429 processor

- 8MHz crystal, USB on PA11/PA12, 32KiB offset

___________________________END OCTOPUS CONFIG OPTIONS___________________________

Press the Q then Y key to commit CanBoot config.

make

You have now created a canboot.bin firmware file for your Octopus board. My approach is to now make the CanBoot firmware for the EBB board. But if you do this now it will override the Octopus firmware you just created. So do the following:

On your computer, open a Windows CMD terminal

Type: pscp -C pi@<IP_ADDRESS>:/home/pi/CanBoot/out/canboot.bin octopus_canboot.bin

- Make sure to replace <IP_ADDRESS> with your Pi IP address or network name, like fluiddpi.local

NOTE: You can also manually move the canboot.bin file to your computer with WinSCP. Make sure to name it octopus_canboot.bin (or similar). We will be moving an ebb_canboot.bin file next.

…Back to the Raspberry Pi SSH terminal

make clean

make menuconfig

EBB36 / EBB42 v1.0 with F072 processor

- 8MHz crystal, CAN bus on PB8/PB9, 8KiB offset, 500000 CAN bus speed

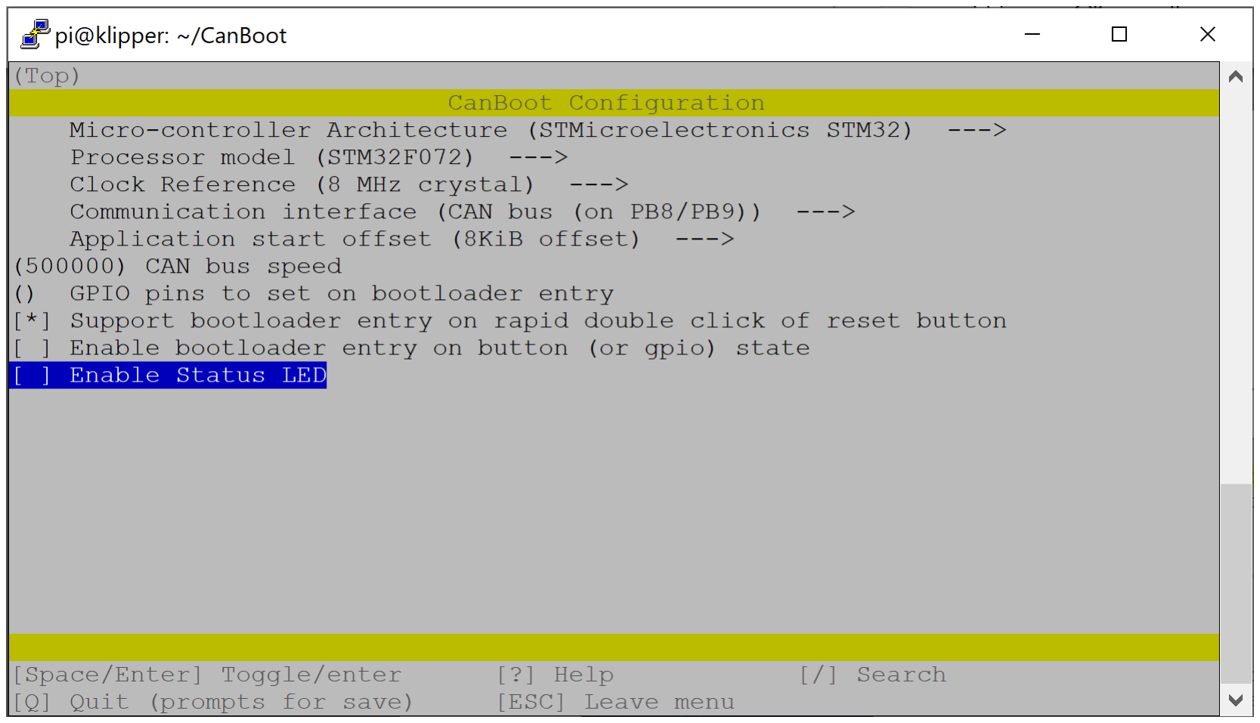
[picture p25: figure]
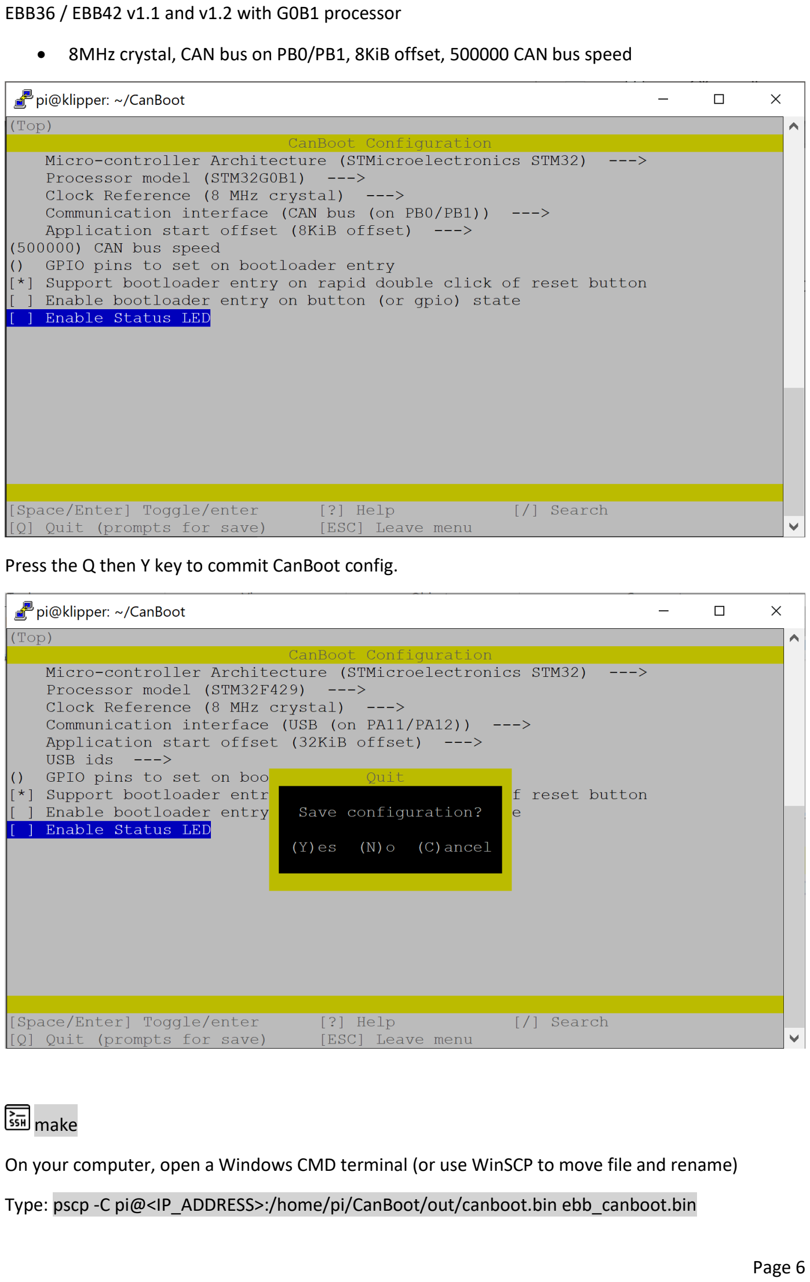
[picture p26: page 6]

EBB36 / EBB42 v1.1 and v1.2 with G0B1 processor

- 8MHz crystal, CAN bus on PB0/PB1, 8KiB offset, 500000 CAN bus speed

Press the Q then Y key to commit CanBoot config.

make

On your computer, open a Windows CMD terminal (or use WinSCP to move file and rename)

Type: pscp -C pi@<IP_ADDRESS>:/home/pi/CanBoot/out/canboot.bin ebb_canboot.bin

- Make sure to replace <IP_ADDRESS> with your Pi IP address or network name, like fluiddpi.local

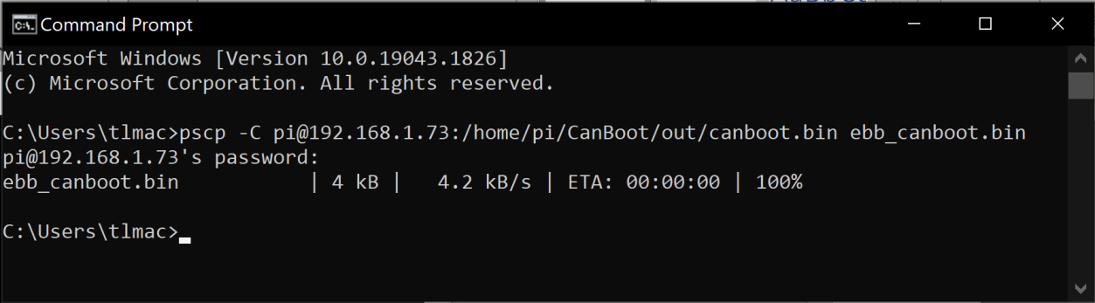
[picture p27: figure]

Your two CanBoot firmware files are now on your computer (in your user folder). Next step is to flash CanBoot to your boards.

1b. Flash CanBoot using STM32CubeProgrammer

You’ll need to put your boards into DFU mode and connect to the computer using a USB-A to USB-C cable. Boot instructions for the Octopus and Octopus Pro are below:

Make sure the power is off to the Octopus board

- To start have the USB-C to USB-A cable connected between the Windows PC and the Octopus Board.
- Remove the USB-C power jumper and place a jumper on the Boot0 header.

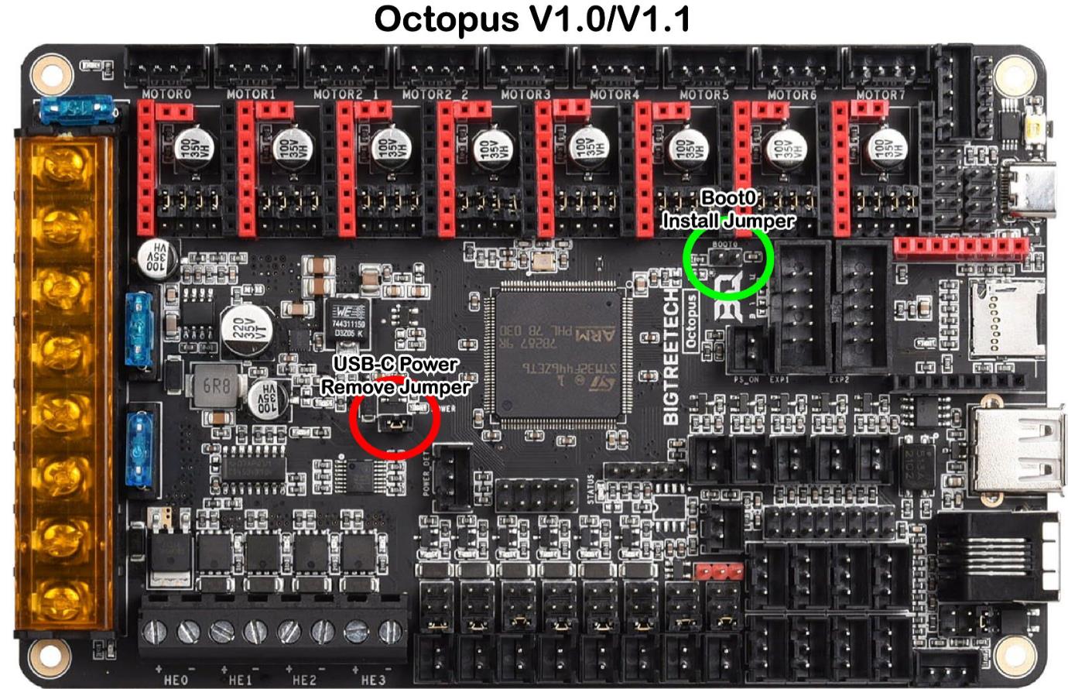
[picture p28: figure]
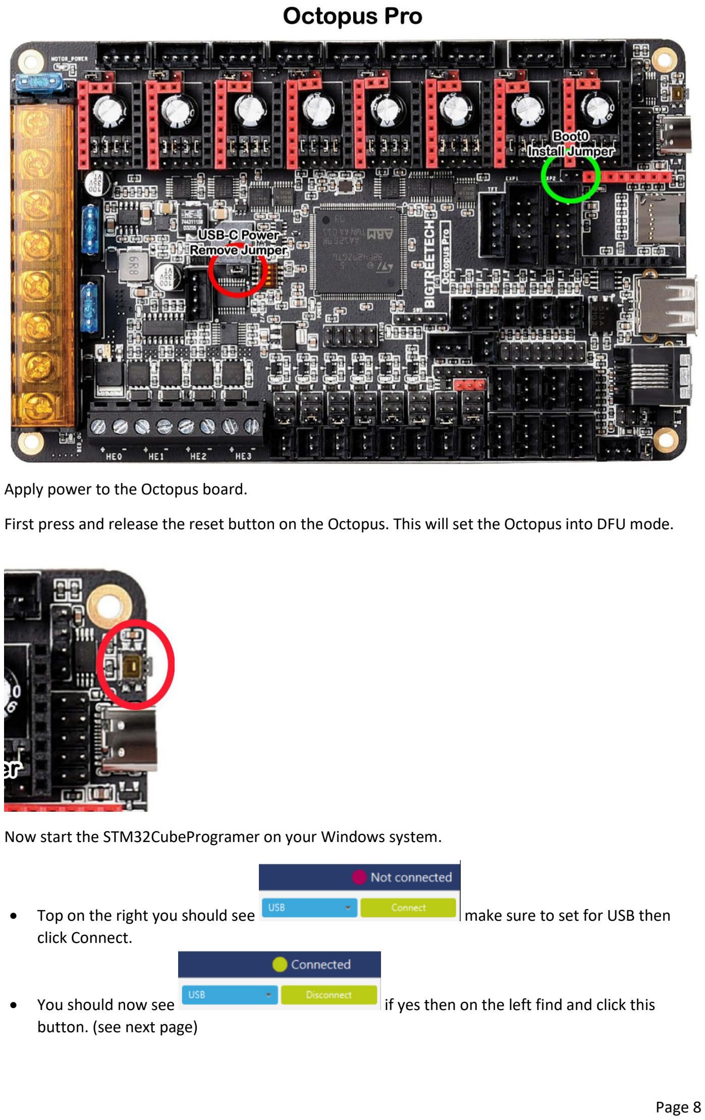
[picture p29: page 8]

Apply power to the Octopus board.

First press and release the reset button on the Octopus. This will set the Octopus into DFU mode.

Now start the STM32CubeProgramer on your Windows system.

- | Top on the right you should see | make sure to set for USB then
| click Connect.
- | You should now see | if yes then on the left find and click this
| button. (see next page)

- For CanBoot and Klipper to work correctly we need to wipe the flash memory by clicking this button.

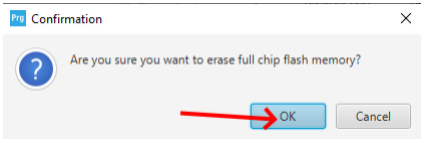
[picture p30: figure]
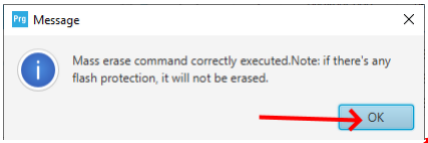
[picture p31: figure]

- Go back to main page by clicking on this button

- Select (1) “Open File” tab, find the octopus_canboot.bin file, and (2) download to your Octopus board. (3) Click Disconnect when done.

Power off your Octopus board. Remove the jumper from BOOT0.

Now you’ll flash your EBB toolboard.

This step will power the toolboard from USB only. Place a jumper on VBUS header.

EBB36 / EBB42 v1.0

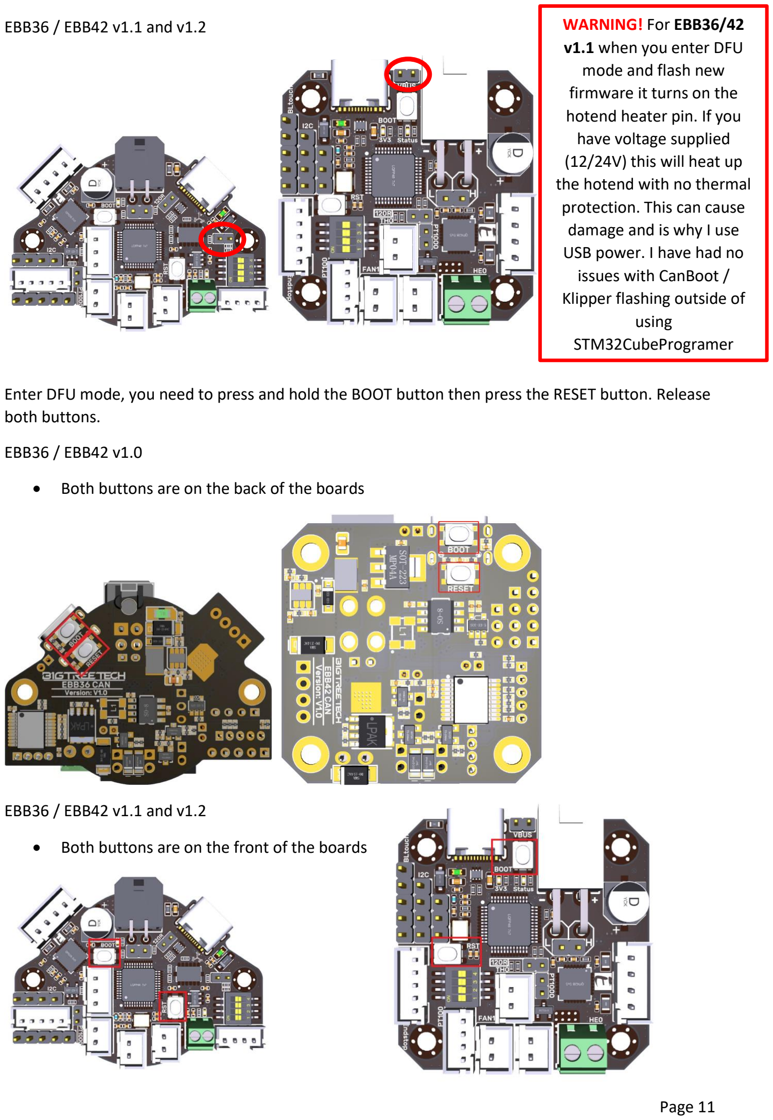
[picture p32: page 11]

EBB36 / EBB42 v1.1 and v1.2

Enter DFU mode, you need to press and hold the BOOT button then press the RESET button. Release both buttons.

EBB36 / EBB42 v1.0

- Both buttons are on the back of the boards

EBB36 / EBB42 v1.1 and v1.2

- Both buttons are on the front of the boards

WARNING! For EBB36/42
v1.1 when you enter DFU
mode and flash new
firmware it turns on the
hotend heater pin. If you
have voltage supplied
(12/24V) this will heat up the hotend with no thermal protection. This can cause damage and is why I use
USB power. I have had no
issues with CanBoot /
Klipper flashing outside of using
STM32CubeProgramer

Now start the STM32CubeProgramer on your Windows system.

- | Top on the right you should see | make sure to set for USB then
| click Connect.
- | You should now see | if yes then on the left find and click this
| button.
- For CanBoot and Klipper to work correctly we need to wipe the flash memory by clicking this button.

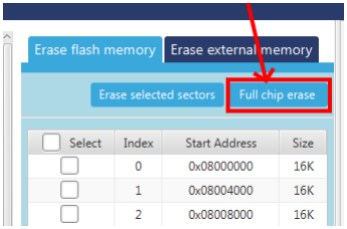
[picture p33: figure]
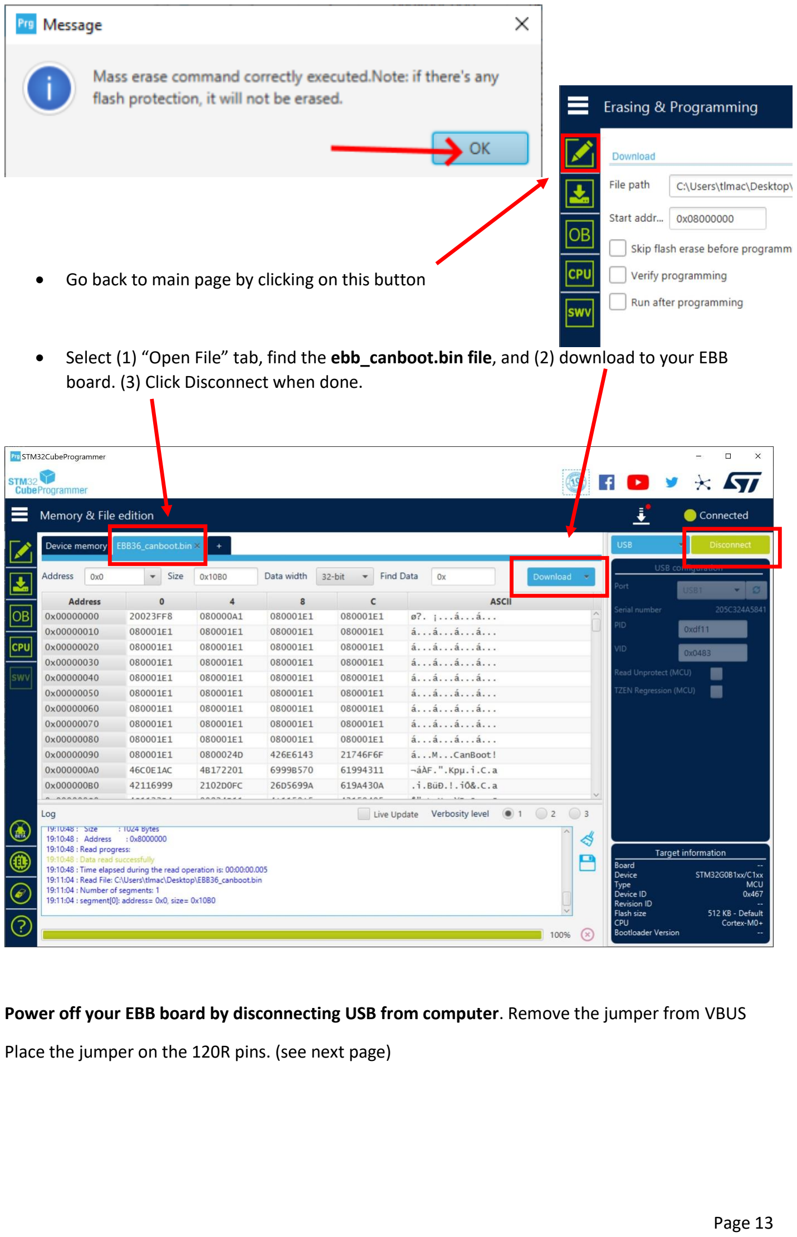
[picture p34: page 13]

- Go back to main page by clicking on this button
- Select (1) “Open File” tab, find the ebb_canboot.bin file, and (2) download to your EBB board. (3) Click Disconnect when done.

Power off your EBB board by disconnecting USB from computer. Remove the jumper from VBUS

Place the jumper on the 120R pins. (see next page)

EBB36 / EBB42 v1.0

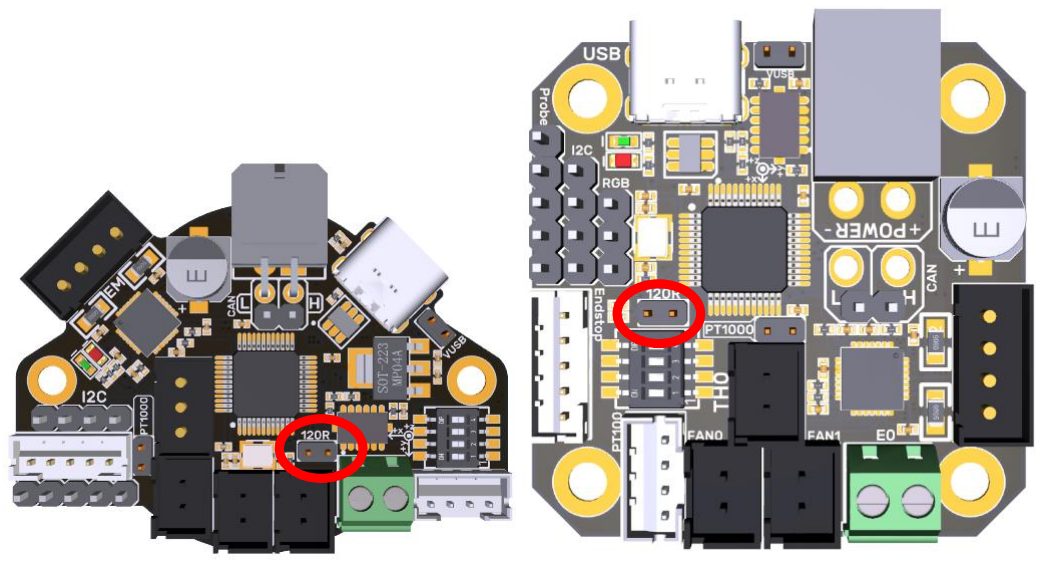
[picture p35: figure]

EBB36 / EBB42 v1.1 and v1.2

Set aside the EBB toolboard for now.

2. Setup Octopus / Pro for Klipper

Go back to your SSH terminal window.

cd ~/klipper

make menuconfig

2a. Octopus - Setup Klipper for USB to CAN bus bridge, with CAN comms to EBB

You will now setup the new USB to CAN bus bridge on your Octopus / Pro board. Below are the Klipper config options for each board. Make sure to have “Enable extra low-level configuration options” selected.

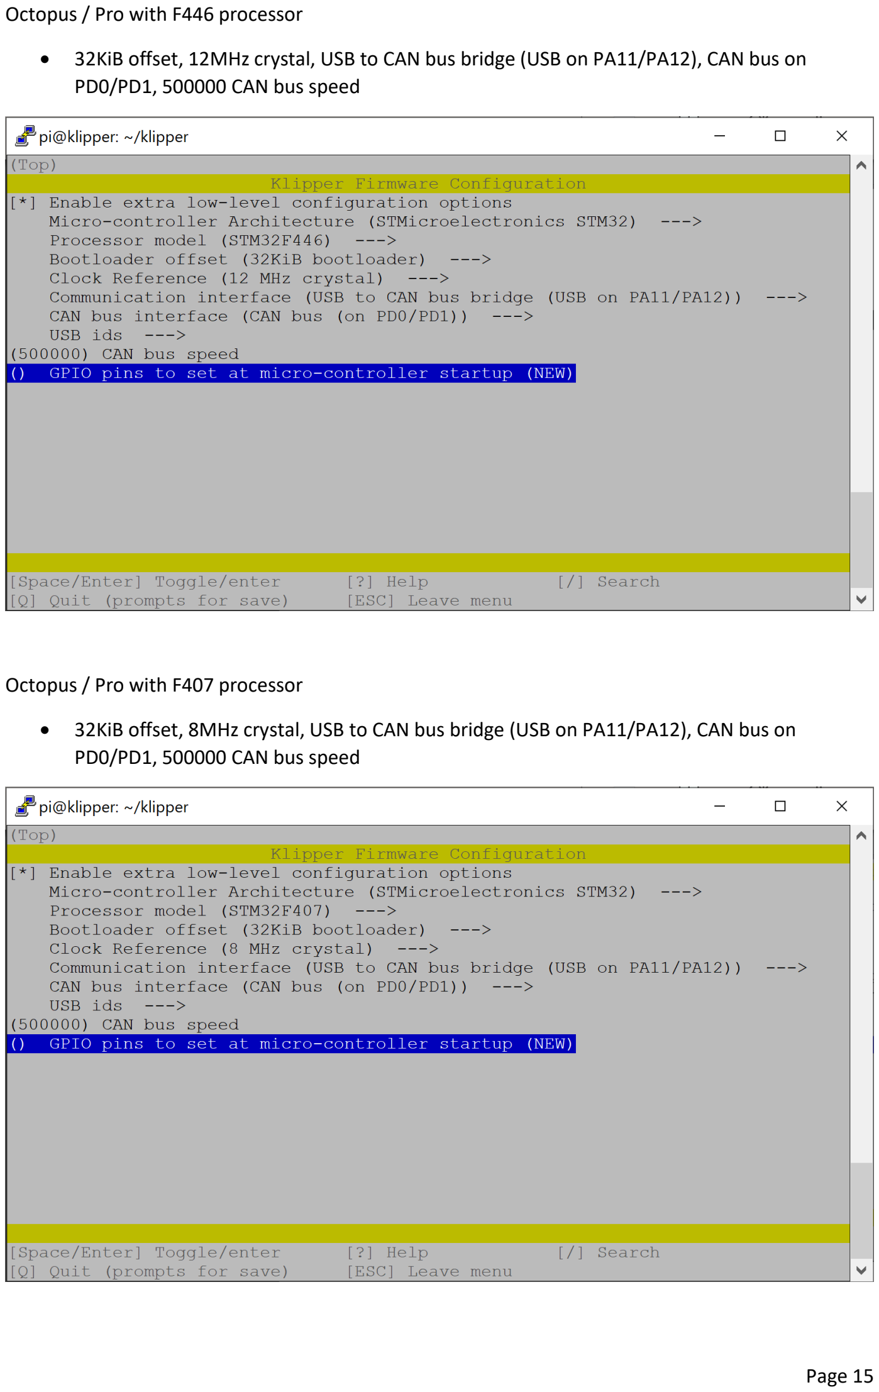
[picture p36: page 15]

Octopus / Pro with F446 processor

- 32KiB offset, 12MHz crystal, USB to CAN bus bridge (USB on PA11/PA12), CAN bus on PD0/PD1, 500000 CAN bus speed

Octopus / Pro with F407 processor

- 32KiB offset, 8MHz crystal, USB to CAN bus bridge (USB on PA11/PA12), CAN bus on PD0/PD1, 500000 CAN bus speed

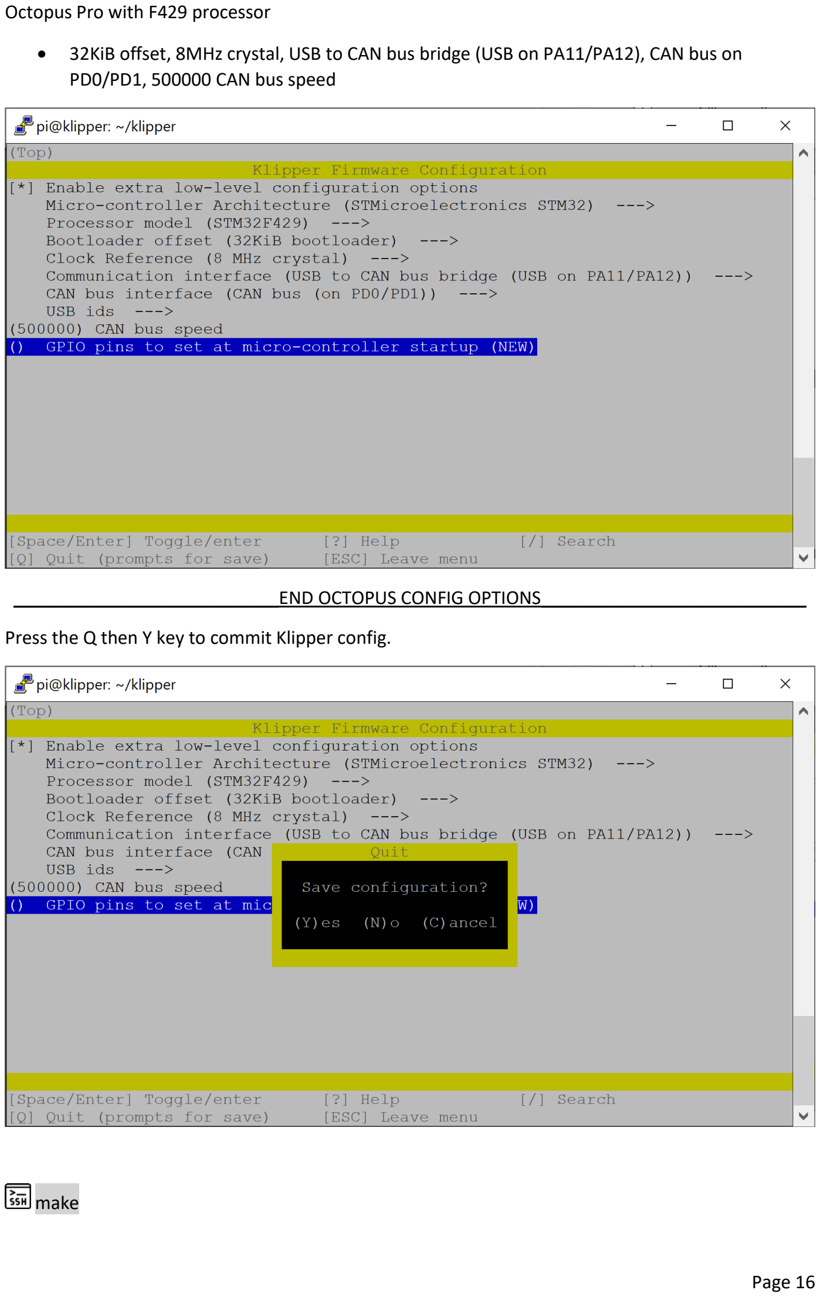
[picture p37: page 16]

Octopus Pro with F429 processor

- 32KiB offset, 8MHz crystal, USB to CAN bus bridge (USB on PA11/PA12), CAN bus on PD0/PD1, 500000 CAN bus speed

___________________________END OCTOPUS CONFIG OPTIONS___________________________

Press the Q then Y key to commit Klipper config.

make

NOTE:

Just like with the CanBoot firmware we will be making Klipper firmware for the Octopus / Pro board and the EBB board. Since we are already compiling Klipper firmware, I like to compile the EBB Klipper firmware now. But if we do, then the Octopus Klipper firmware we just made will be overwritten. So:

mv ~/klipper/out/klipper.bin octopus_klipper.bin

make clean

NOTE:

This moves the klipper firmware file to the klipper folder and renames it octopus_klipper.bin then deletes the compile files and folders, including /klipper/out

2b. EBB - Setup Klipper for CAN comms

make menuconfig

EBB36 / EBB42 v1.0 with F072 processor

- 8KiB bootloader, 8MHz crystal, CAN bus on PB8/PB9, 500000 CAN bus speed

EBB36 / EBB42 v1.1 / v1.2 with G0B1 processor

- 8KiB bootloader, 8MHz crystal, CAN bus on PB0/PB1, 500000 CAN bus speed

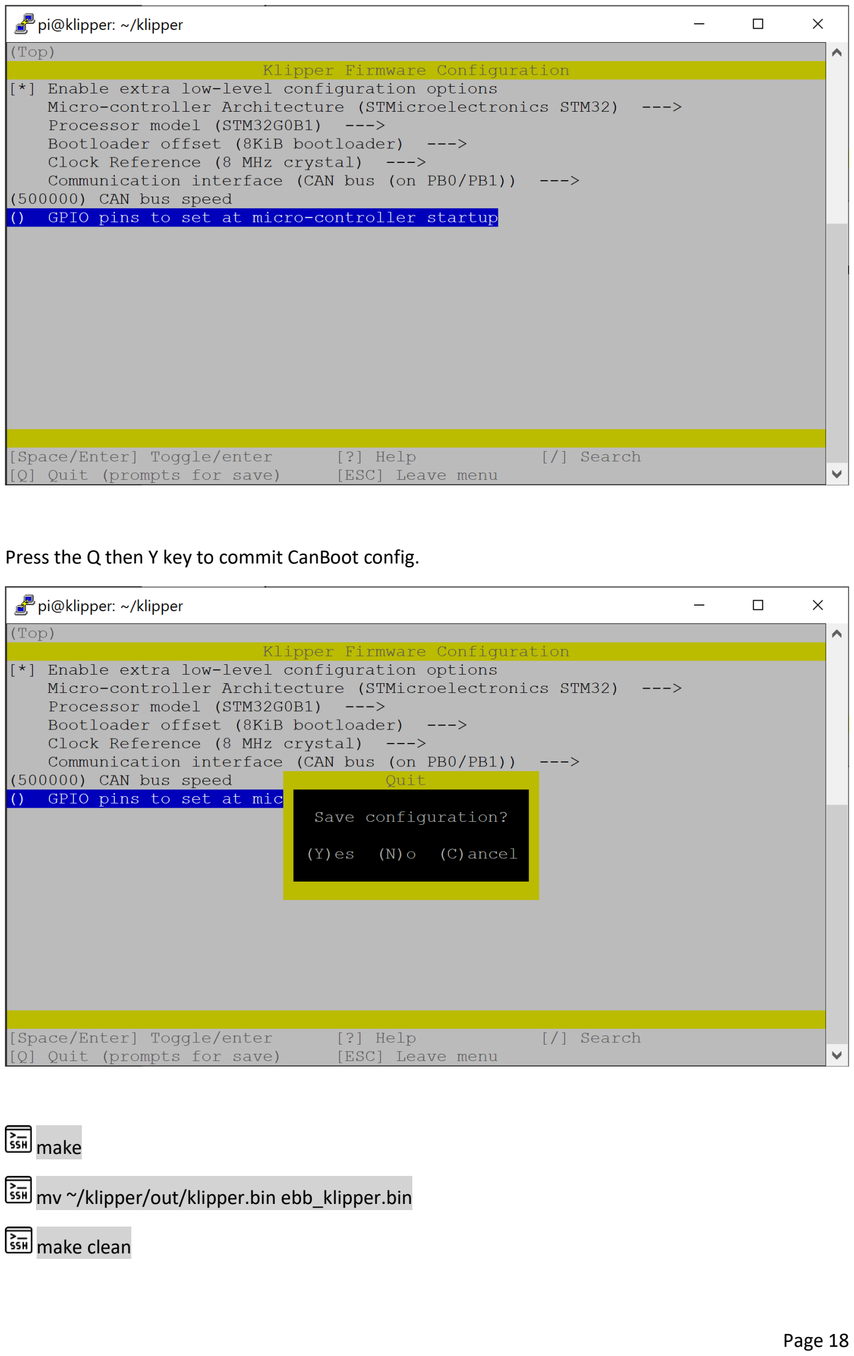
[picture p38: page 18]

Press the Q then Y key to commit CanBoot config.

make

mv ~/klipper/out/klipper.bin ebb_klipper.bin

make clean

2c. Find serial device for Octopus / Pro on Raspberry Pi

Connect your Octopus / Pro board to the Raspberry Pi with a USB-A to USB-C cable…connected to the USB-C port on the Octopus board. Power on your printer.

cd

ls /dev/serial/by-id/*

This will give you something similar to below. YOUR DEVICE WILL BE DIFFERENT!

Copy this, for example:

/dev/serial/by-id/usb-CanBoot_stm32f429xx_350026000B50314B33323220-if00

2d. Flash Klipper to Octopus / Pro with CanBoot serial command

cd CanBoot/scripts

pip3 install pyserial

…this only has to be done once

python3 flash_can.py -f ~/klipper/octopus_klipper.bin -d <serial_device>

NOTE: Replace <serial_device> with the path you copied earlier…

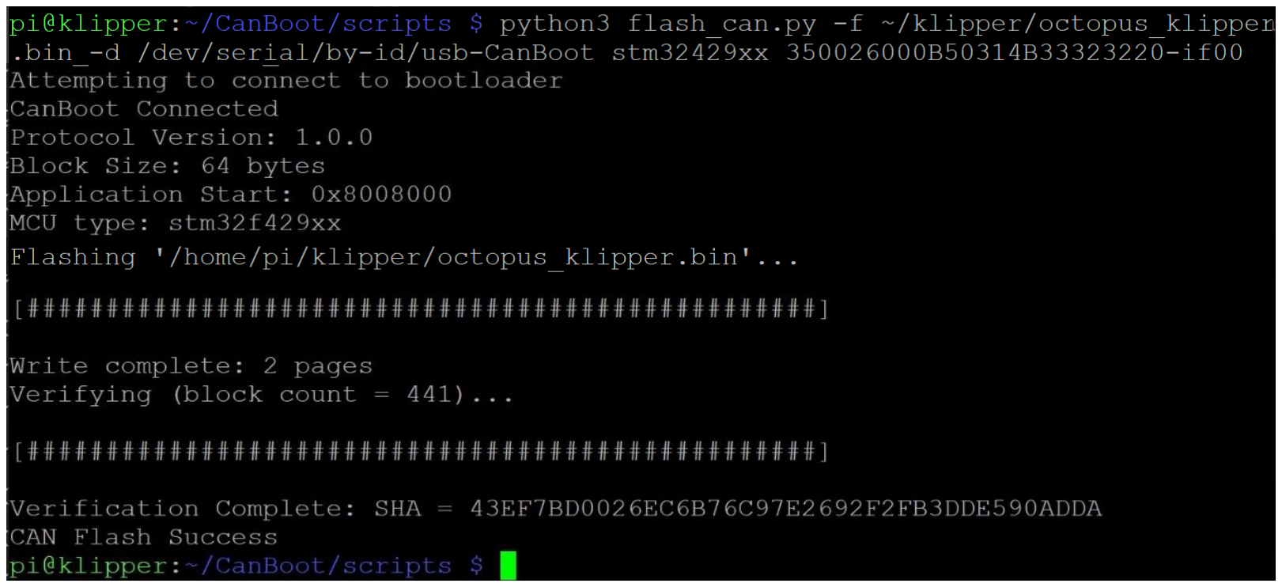
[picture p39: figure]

NOTE: The Octopus board communicates over USB initially. Only this flash (and Klipper updates, more on that later) use the serial device path. The Octopus board now has a CAN uuid…let’s find it!

3. Setup can0 Network on Raspberry Pi, Power Cycle Printer

Now we need to enable the can0 network and set it up so that we can have CAN bus working

cd

sudo nano /etc/network/interfaces.d/can0

- Copy and paste the following:

allow-hotplug can0
iface can0 can static
bitrate 500000
up ifconfig $IFACE txqueuelen 128

Ctrl – X to EXIT.

Key Y for YES, and ENTER.

Power off your printer. Time to plug in your EBB toolboard. Plug power and can data cables into EBB. Plug RJ11 or RJ12 connector into Octopus / Pro board.

Power on your printer.

NOTE:

We just created the can0 interface as a hot-plug network. This means that when something changes to devices, or new devices are connected, the network reacts. Power cycling the printer is a change that the can0 network detects and configures the Octopus to work as a CAN device. Also, this hot-plug option seems to make “firmware_restarts” smoother.

4. Find CAN uuid for Octopus / Pro

Now that can0 is setup, let’s make sure it is up and running.

ifconfig

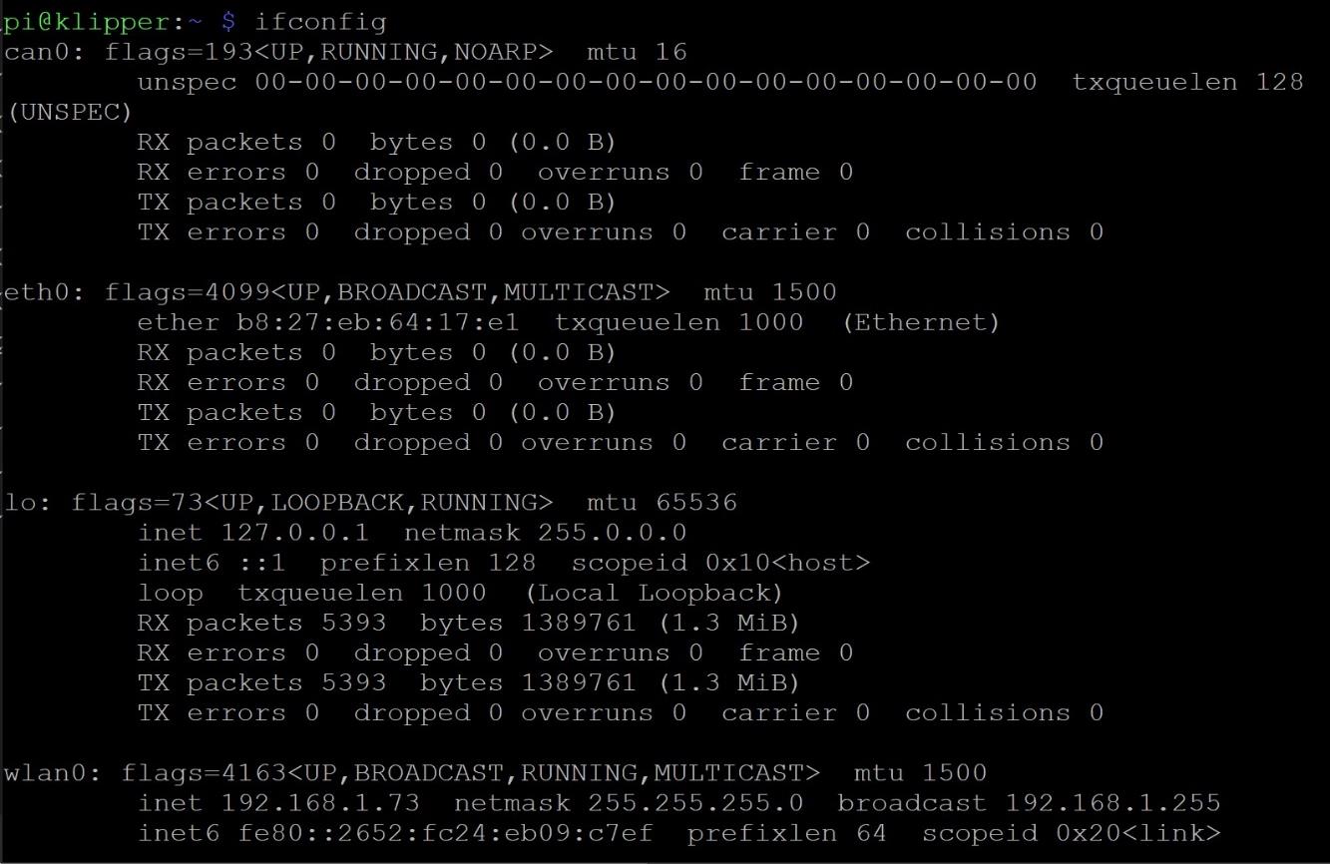
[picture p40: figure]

You should get results similar to this. We are looking for the can0 on top. Success!

NOTE: If this doesn’t work try to turn off power to your printer and reboot your Raspberry Pi. Wont booted back up, open a SSH terminal and try ifconfig again. Can0 won’t show up. Power on your printer and then try ifconfig. Should have can0 up and running.

cd CanBoot/scripts

python3 flash_can.py -i can0 -q

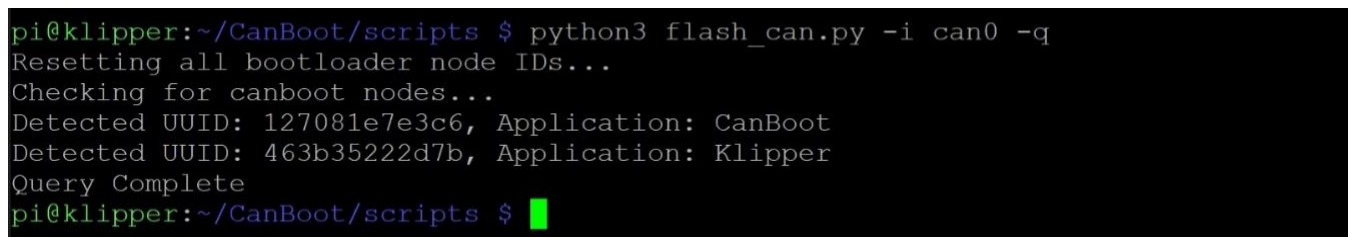
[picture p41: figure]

In this instance both EBB and Octopus are detected. The EBB only has CanBoot on it while the Octopus has Klipper. It is obvious which is which. Save both for later.

5. Flash Klipper to EBB board with CanBoot CAN command

python3 flash_can.py -f ~/klipper/ebb_klipper.bin -u <ebb_uuid>

NOTE: Replace <ebb_uuid> with the CAN uuid found before. The EBB is labelled with “CanBoot”. In this case mine is 127081e7e3c6

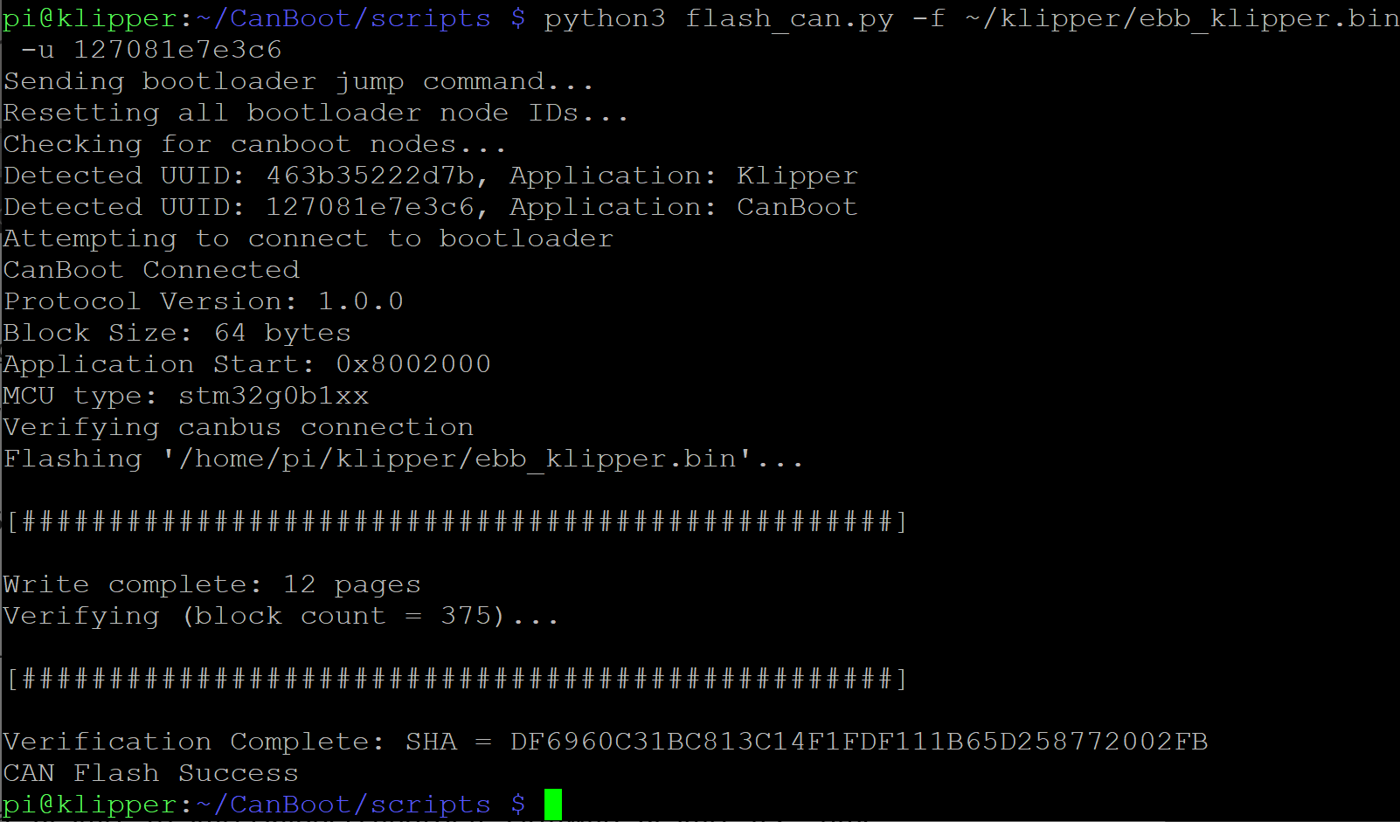
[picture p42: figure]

cd ~/klipper

rm octopus_klipper.bin ebb_klipper.bin

6. Printer Config Update and General Tips

Edit your printer.cfg to now include your new CAN uuid. For example:

[mcu]
canbus_uuid: 463b35222d7b

[mcu EBBCan]
canbus_uuid: 127081e7e3c6

Save and restart.

If you have issues here, try a “Restart” (restarts Klipper) and/or a “Firmware Restart” a 2nd time.

- The issue is can0 network disconnects when the restart causes a power cycle on your printer. The timing can be too fast and the can0 network doesn’t properly come back up. Another restart command is sometimes needed.
- | According to Klipper CANBUS docs, you might need to issue | sudo ip up in a SSH terminal to
restart the can0 network. I haven’t had to do this. But this might be useful during initial setup.

- | You can also use | sudo ip link set up can0 type can bitrate 500000 in a SSH terminal to start
can0 if it isn’t coming up with ifconfig. I have used this, but find that if the install instructions are followed then I don’t need it.
- See Klipper docs on CANBUS for official information https://www.klipper3d.org/CANBUS.html#usb-to-can-bus-bridge-mode
7. How to Use CanBoot to update boards, Tips

With CanBoot and Klipper now properly flashed to your Octopus / Pro board and EBB toolboard you now have two devices with unique CAN uuid on can0 network. But how to use CanBoot to upgrade Klipper firmware!?

When you run python3 flash_can.py | the python script should trigger the board to go into DFU
mode, to access CanBoot on the board and flash the Klipper update. I can’t cleanly get this to work with my Octopus Pro with F429 processor.
- Flashing with CAN uuid gives an error. Trying to use the original serial ID also gives an error.
- How I get it to work:
- Make Klipper firmware for Octopus board, cd to CanBoot/scripts
- I run: python3 flash_can.py -f ~/klipper/octopus_klipper.bin -u 463b35222d7b
- Note I am still moving and renaming firmware files. If you don’t want to do this then leave out: -f ~/klipper/octopus_klipper.bin and CanBoot defaults to using default location of Klipper firmware [ ~/klipper/out/klipper.bin ]
- CanBoot throws an error. If I try ifconfig, the can0 network is down
- Now if I try ls /dev/serial/by-id/* I get a serial ID:
- /dev/serial/by-id/usb-CanBoot_stm32f429xx_350026000B50314B33323220-if00
- Same as earlier…
- Now I run:
- python3 flash_can.py -f ~/klipper/octopus_klipper.bin -d /dev/serial/by-id/usb-CanBoot_stm32f429xx_350026000B50314B33323220-if00
- And CanBoot works and flashes Klipper update!
- I can now update the EBB with: python3 flash_can.py -f ~/klipper/ebb_klipper.bin -u 127081e7e3c6

Long story short;

1. Try to flash Octopus board with CAN uuid, it will fail and can0 network is down.
2. Now you can flash Octopus board with serial ID.
3. Lastly you can flash EBB board with CAN uuid.

CAN Bus Wiring on next page…

RJ11 / RJ12 CAN bus Wiring Info

To connect your EBB36/42 or other CAN enabled toolboard directly to the Octopus boards you need to use the RJ11 / RJ12 telephone port.

The easiest option is to use a 2-3 meter telephone cable and cut off one end. Crimp for Molex MiniFit or Molex MicroFit connector, depending on your CAN toolboard. The RJ11/12 connector goes to the Octopus board.

- This does not allow for twisted wire, which is recommended for CAN bus wiring.
- I have the 4 wire RJ11 telephone cable running directly to my EBB36, no twisted wire. No issues on my end but I will work to get twisted wire setup in the future.

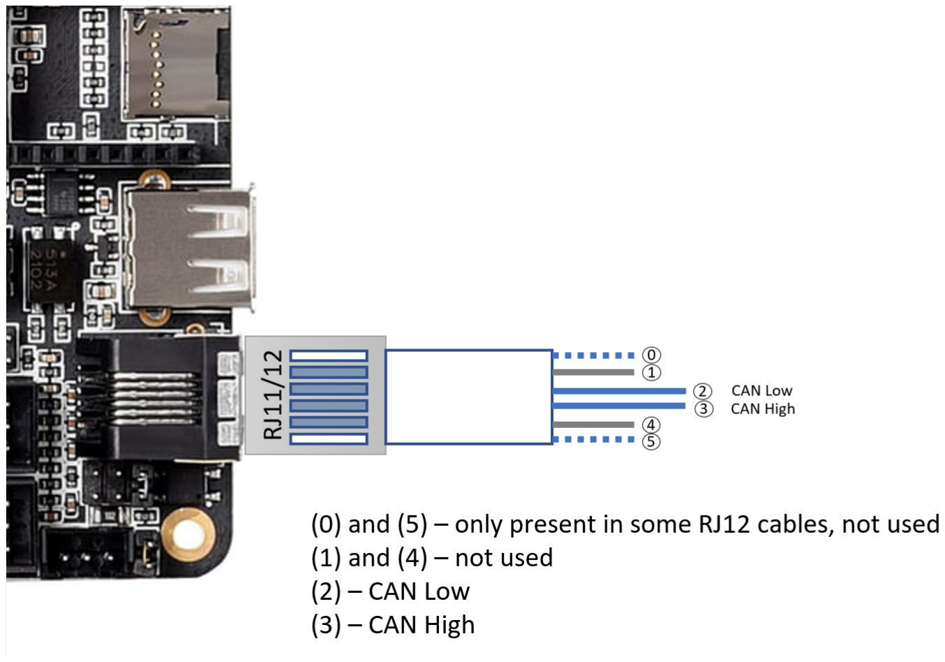
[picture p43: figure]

When you plug in the RJ11/12 cable to the Octopus board, the wiring (from top down) is as above. DO NOT RELY ON WIRE COLOURS. For example:

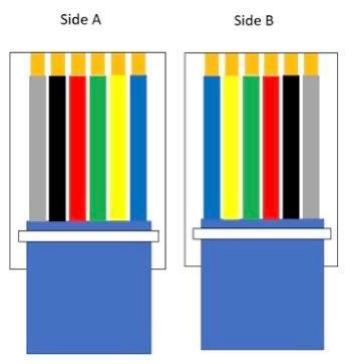
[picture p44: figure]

If plugging in a RJ12 cable with SIDE A your CAN Low wire is GREEN and CAN High wire is RED.

If plugging in a RJ12 cable with SIDE B your CAN Low wire is RED and CAN High wire is GREEN.

The colour of your wiring setup will be situational.

Take note of the wiring that you have plugged into the Octopus board. Wire 2 is your CAN Low connection. Note the colour of the wire and make sure it goes to CAN_L on the EBB end. Same thing for the CAN High on Wire 3. That colour wire goes to CAN_H on the EBB end.

You must also supply 12V or 24V directly to the EBB toolboard. Run 18awg directly from your power supply. Example EBB connections are below. Again, colours on the diagrams do not indicate wire colours.

EBB36

EBB42

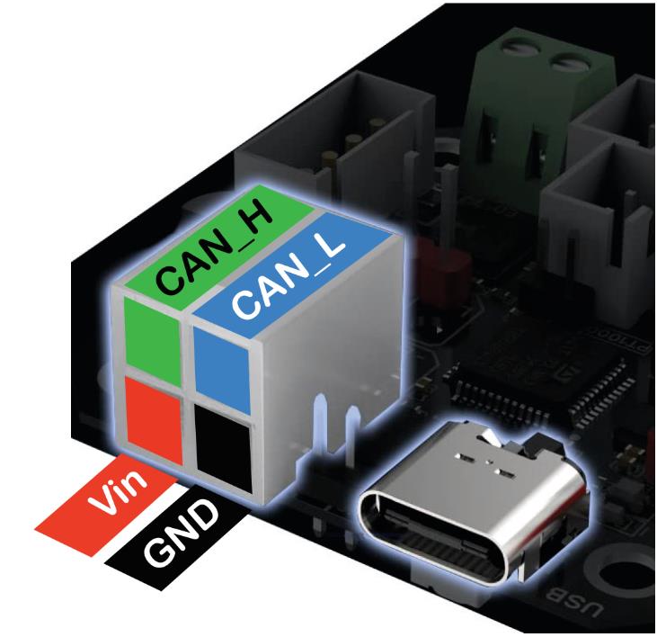
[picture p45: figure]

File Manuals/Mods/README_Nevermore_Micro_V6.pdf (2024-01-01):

SSuuppppoorrtt NNeevveerrmmoorree33DD BBuuyy mmee aa ccooffffeeee (https://www.buymeacoffee.com/nevermore3d)

# Nevermore Micro V6

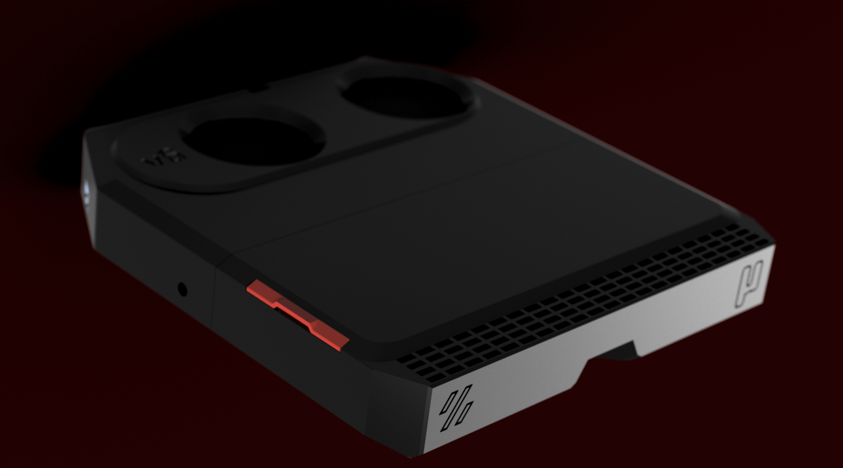
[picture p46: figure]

Nevermore Micro V6 is here! It is designed to supersede both the V4 and V5 duos, which will soon be considered legacy designs.

## What's New?

Intact 5015 Fans: V6 now make use of fully intact 5015 fans, eliminating the need to cut the fan scroll or wires. This raises a concern: does it waste carbon if airflow from a small 15mm 5015 fan exhaust isn't spread over the entire 130mm filter surface? Yes, usually - however, we have overcome this challenge through use of evasees and vanes to efficiently spread the airflow within the small plenum space. This means all the carbon receives airflow immediately, without requiring any fan modifications.

Enhanced Heat Tolerance: Unlike its predecessors, V6 can tolerate higher levels of heat. The V4 and V5 had thinner lids that could bend or warp, especially when subjected to temperatures above 100°C under a heated bed. This sometimes resulted in broken or damaged units. However, the V6 is beefed up to address this issue. With a thicker frame, structured vanes, and lids strategically placed away from the heat source, the chances of melting a Nevermore Micro are significantly reduced.

Improved Airflow: V6 boasts superior airflow. We have achieved this by optimizing the printing direction, which allows for built-in seals. Say goodbye to air leaks between the cartridge and the plenum! Furthermore, the air intakes have been redesigned to accommodate increased airflow. Now, it can process the chamber volume of a 250 Voron in just 30 seconds, and a larger 350 in approximately 2 minutes.

Reduced Noise: V6 generates less noise compared to the V5, thanks to a redesigned air intake.

Compatibility: V6 can be printed on any machine, including on a Voron v0 on which a v5 duo previously wouldnt fit. Yet the size is the same, its dark sorcery.

Sleek Design: V6 not only performs exceptionally but also looks awesome. It features a novel jalousie lid design with no bolts, allowing for convenient one-handed carbon swaps. Gone are the days of dealing with annoying bolts or latches when swapping carbon. Rest assured, this design remains super secure. You have to try it to believe it! Jalousie demo here. (https://youtube.com/shorts/sSmVfhcDKrI?feature=share)

## Print material and settings

Designed and prototyped with ABS materials. Any material that is heat resistant enough for the installation spot will likely work, but brittle material (i.e regular PLA) should be avoided for the jalousie slider and the spring fan fasteners.
Made for standard voron settings. 0.2 mm layer height needed for supports to line up right, and 0.4-0.5mm line width for optimal mesh printing. 5 walls recommended for jalousie structural integrity, otherwise its pretty sturdy regardless.
JALOUSIE can be break if your slicer settings interferes with the intended extrusion path. A suggestion from @Haldamir is to print it with 0 bottom solid, 1 top solid layers, 5 perimeters and 0.4 extrusion width. Also 90 degrees infill angle, so the 3rd layer is printed in this orientation. Avoid bottom horizontal expansion so that there are no large gaps between the parallell length-wise extrusion lines (built in gaps in the bottom and second layer forces the slicer to print in a length-wise paralell pattern. Ideally, you want these gaps to fuse slightly for greatest strength). Some users has reported going slow for the first three layers improves the structural rigidity, as it gives more time for the layers to fully fuse. If your jalousie is prone to crack, try slowing down to 40mm/s and perhaps raise the temp slightly for better fusing. There is also a "thin" jalousie that might be a better fit for stiffer materials. It has bend layers that are 0.4mm instead of 0.6mm, which paradoxically will make a jalousie prone to cracking with bending hold up better.

## BOM and Installation

Support Removal

Before installation, there are a few support pieces that need to be removed:

Plenum:

A long bridge along the top of the cartridge.
The two triangular pillars extending to the fan tab slot from the area around the fan intakes. The top portion of the two fan intakes.
On the bottom right evasee/side bolt mount slot as viewed from the front.

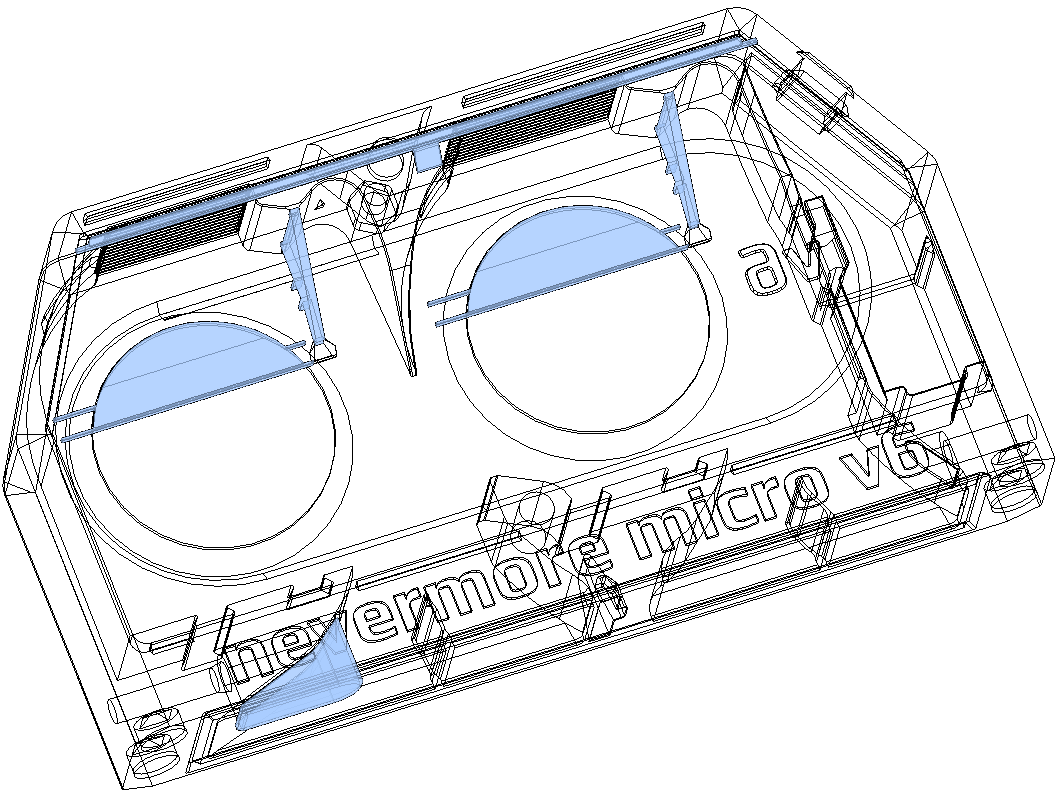
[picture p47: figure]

Cartridge:

The lid/jalousie area has a single support piece. Be cautious when removing it, ensuring not to damage the jalousie sliding path. If the support is fused, use an X-Acto knife if necessary.

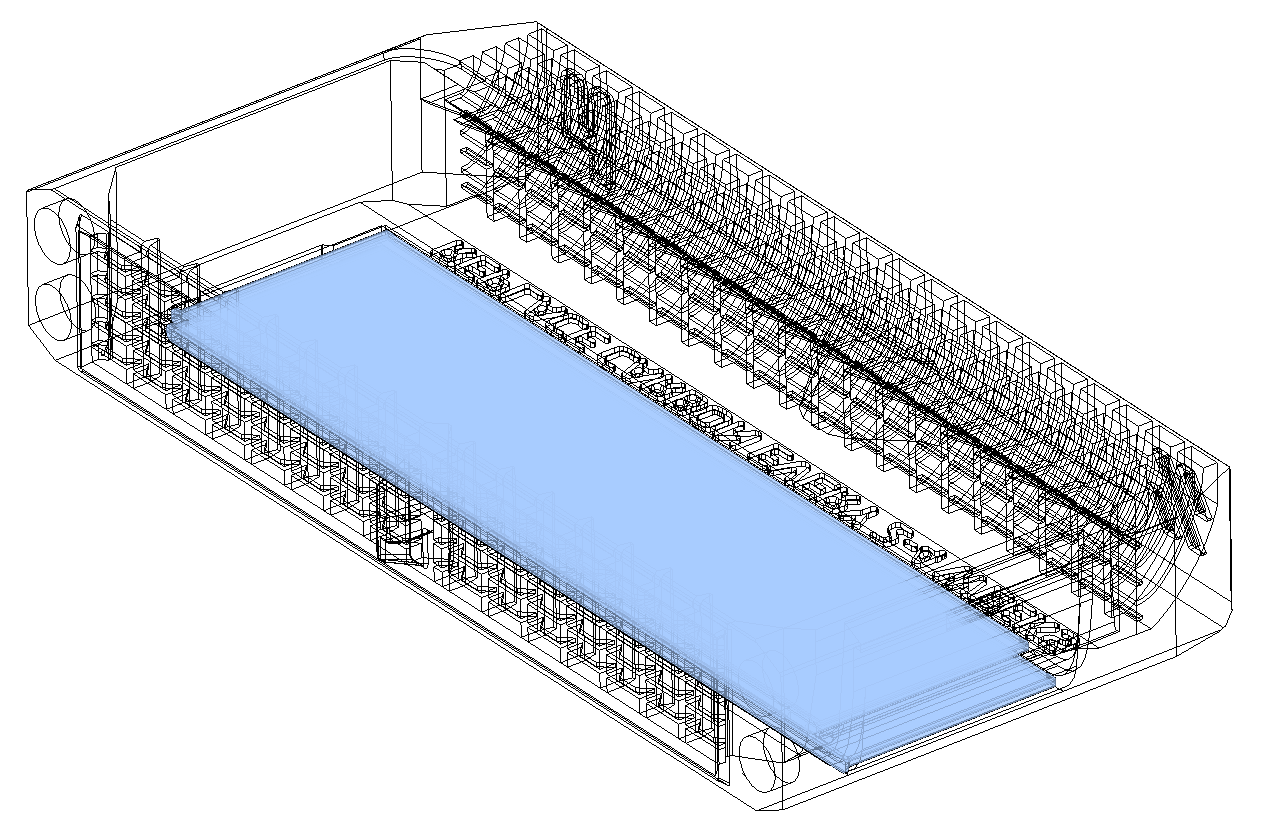
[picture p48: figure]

Plenum

Electronics

Required:

2x 5015 blowers (compatible with Delta, Honeybadger, Gdstime, and Winsin. Sunons might fit but the intake holes may not line up perfectly). It is recommended to use blowers with good static pressure (>150Pa).

Wiring Options:

. Single JST-XH 2-pin: Solder both fan wires to a single JST-XH 2-pin connector and connect it to the plenum port.
. Triple JST-XH 2-pin: Print the [2xJST_Holder.stl] insert to create a triple JST-XH 2-pin port. Connect the fans without cutting fan wires by daisy-chaining the 2 extra JST connectors to the plenum JST port. Note that for thicker and longer fan wires (like Gdstime), the wiring space may need to be completely filled with wire.
. Dual WAGO 221 2-pin connectors: Cut the fan wires, twist the fan wires together (12V bundle + GND bundle), and use WAGO connectors as wire extensions. Print the [Wire_connector.stl] that fits the plenum JST port. Insert the power wire from your printer and connect it to the corresponding WAGO socket. Lastly, insert the WAGO connectors into their slots.

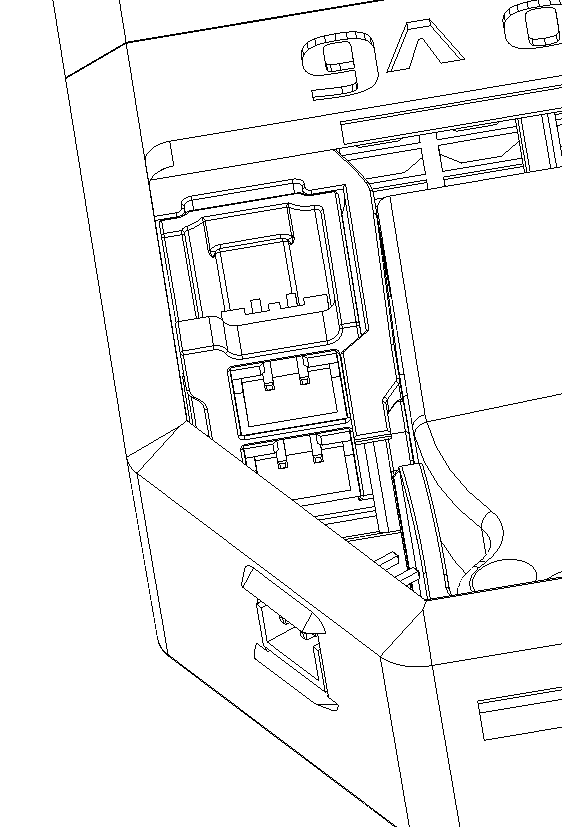
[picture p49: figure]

TRIPLE-JST and WAGO

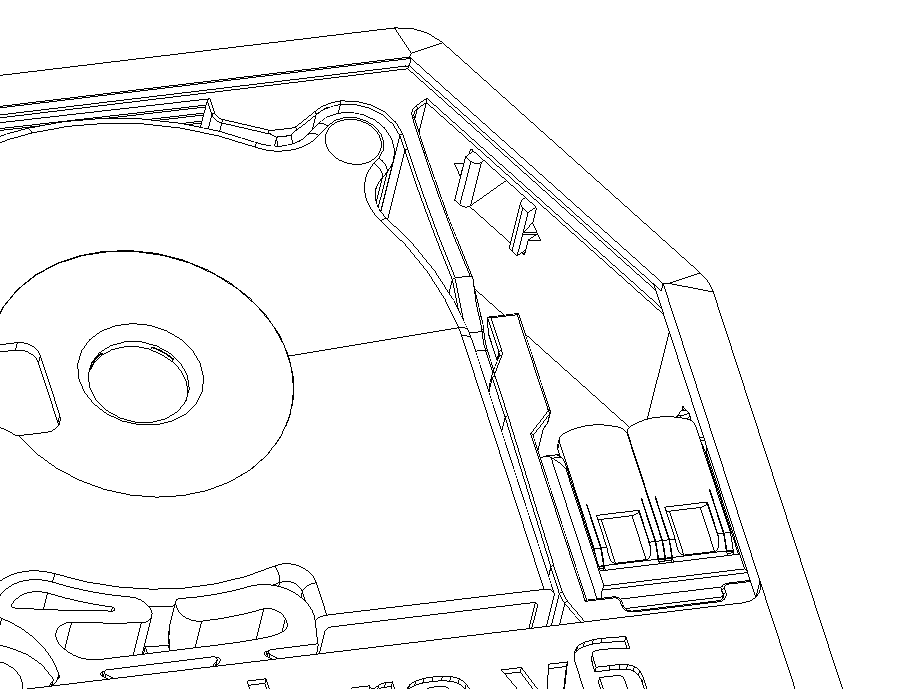
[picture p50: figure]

Magnets

Required:

4x 6mm wide and 3mm deep magnets (also 4x magnets on the cartridge side, totaling 8 magnets). Note: Take care when installing the magnets. A common issue is getting polarity wrong.

Plenum Wiring and Lid Install

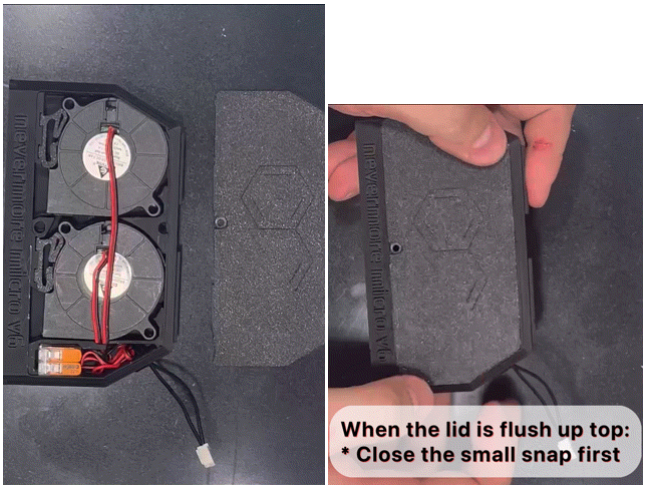
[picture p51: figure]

Back Extrusion Mounting

For the V0 1515 version or Trident 2020 version:

Insert 2x M3x4x5 heat inserts, one in the back slot after lid installation, and one to secure the lid fully after snap fitting it.
Use an extrusion T-nut.
Seat [2020_Frame_Connector.stl] OR [1515_Frame_Connector.stl] into the extrusion T-nut with an M3x6mm SHCS.
Slide the plenum over the extrusion connector and connect the pieces with one M3x16 SHCS from the front side of the plenum.

Bed Extrusion Mounting

For the V2 2020 version (or sometimes the Trident 2020 bracket):

Insert 1x M3x4x5 heat inserts, to secure the lid fully after snap fitting it (or both inserts as per above if you plan on using one back, and one side mount)
2x extrusion T-nuts.
1x m3x16 SHCS (left side mount when viewed from top/exhaust)
1x m3x20 SHCS (right side mount mwhen viewed from top/exhaust)
Bolt the V6 to an extrusion t-nut on both side of the filter when mounting under the bed on a v2. Note: Bed doesnt have to be removed; connect the wires and bolt the plenum at the front of the bed, then loosen the bolts by half a turn allowing you to slide it in to position. Once in the right position, tighten it gently with a ball type driver.

Cartridge

Magnets

Required:

4x 6mm wide and 3mm deep magnets (also 4x magnets on the plenum side, totaling 8 magnets).

Jalousie Sliding Lid Installation

The jalousie slider can be printed in any non-brittle yet rigid material. ABS, ABS+, Nylons, PETG, and Tough PLA are suitable options. However, avoid using brittle PLA or TPU.

For the first installation, heat the jalousie slider slightly (for instance, by placing it on the 3D printer's heated bed just below the glass transition temperature for a minute or two). Then, insert it from the top, ensuring the matching orientation, and push it in a few millimeters at a time. The critical moment is the first bend on the first insert, so provide support and help it bend on the opposite side of insertion to prevent cracking or damaging the sliding path. Once inserted, slide it in and out a few times to smooth out any surface imperfections that may hinder smooth operation. Lubrication should not be necessary but can be an option if desired.

## Support My Work

If you find my work helpful, consider buying me some filament 🖍 (https://www.buymeacoffee.com/nevermore3d) .
For more information and documentation, visit our GitHub page. (https://github.com/nevermore3d)

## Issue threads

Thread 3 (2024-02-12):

Fix the dimensions of the top panel

ppak10, 2024-02-12:
The top panel is too small on the x and y by just a little bit and falls in between the 2020 extrusions

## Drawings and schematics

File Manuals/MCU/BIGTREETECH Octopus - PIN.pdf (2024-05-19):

# ART FILM - TOP_TEXT

## MOTOR0

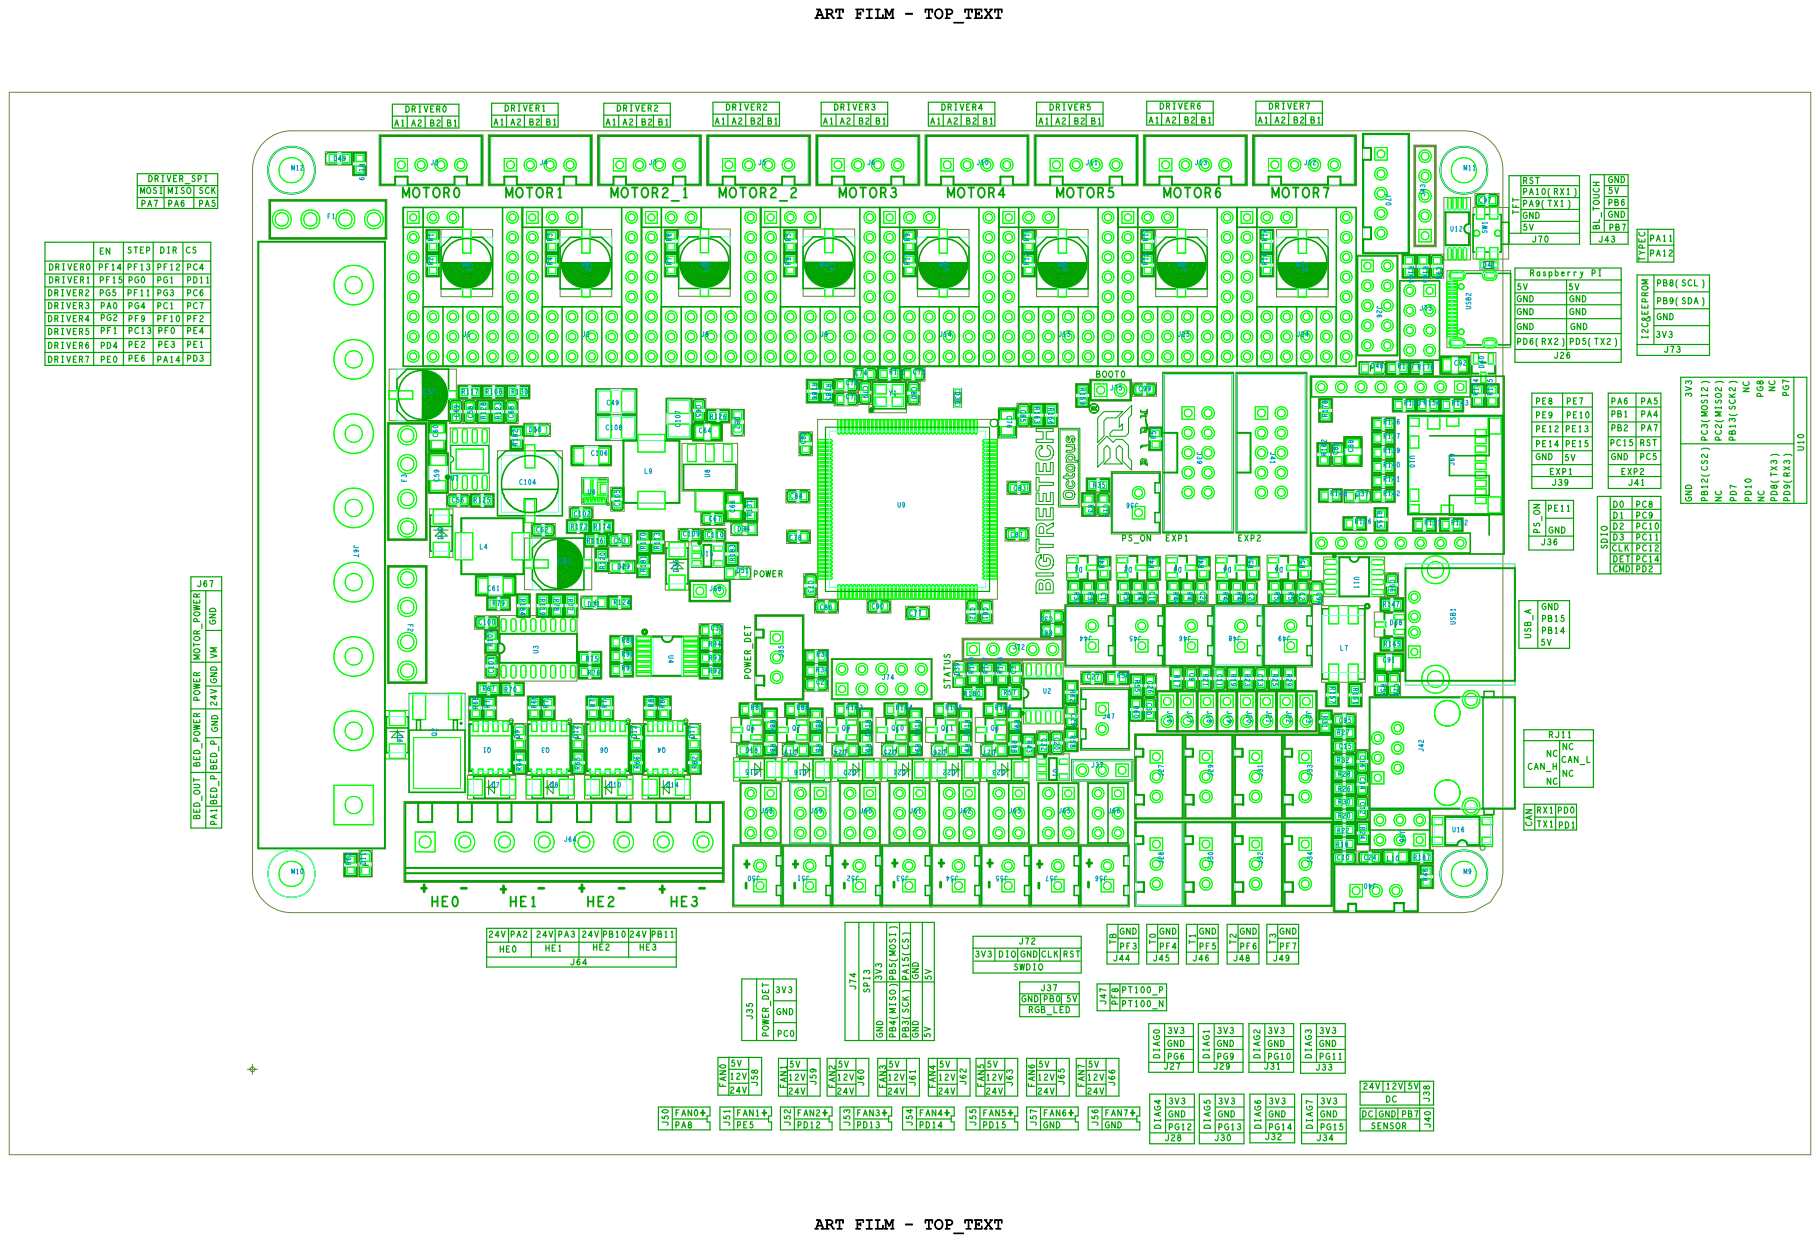
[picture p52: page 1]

MOSI | MISO | SCK

DRIVER1 | PF15 | PG0 | PG1 | PD11
DRIVER2 | PG5 | PF11 | PG3 | PC6
DRIVER3 | PA0 | PG4 | PC1 | PC7

DRIVER5 | PF1 | PC13 | PF0 | PE4

DRIVER6 | PD4 | PE2 | PE3 | PE1

DRIVER7 | PE0 | PE6 | PA14 | PD3

24V | PA2 | 24V | PA3 | 24V | PB10 | 24V | PB11
HE0 | | HE1 | | HE2 | | HE3

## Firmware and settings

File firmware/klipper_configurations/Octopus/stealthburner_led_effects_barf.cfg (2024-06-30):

# Macros for setting the status leds on the Voron StealthBurner toolhead (or for any neopixel-type leds).
#
# You will need to configure a neopixel (or other addressable led, such as dotstar). See
# https://www.klipper3d.org/Config_Reference.html#neopixel for configuration details.


#####################################
#           INSTRUCTIONS            #
#####################################
# How to use all this stuff:
#
#     1.  Copy this .cfg file into your Klipper config directory and then add [include stealthburner_leds.cfg]
#         to the top of your printer.cfg in order for register the LEDs and macros with Klipper.
#     2.  Define your LEDs by editing [neopixel sb_leds] below and entering the data pin from your control board
#         as well as the color order.
#
#           Note: RGB and RGBW are different and must be defined explicitly.  RGB and RGBW are also not able to 
#                 be mix-and-matched in the same chain. A separate data line would be needed for proper functioning.
#
#                 RGBW LEDs will have a visible yellow-ish phosphor section to the chip.  If your LEDs do not have
#                 this yellow portion, you have RGB LEDs.
#
#     3.  Save your config and restart Klipper.
#
#           Note: We set RED and BLUE to 1.0 to make it easier for users and supporters to detect 
#                 misconfigurations or miswiring. The default color format is for Neopixels with a dedicated 
#                 white LED. On startup, all three SB LEDs should light up.
#
#                 If you get random colors across your LEDs, change the color_order to GRB and restart. Then
#                 omit the W for each suggested color_order in the next paragraph.
#
#                 If you get MAGENTA, your  color order is correct. If you get CYAN, you need to use RGBW. If
#                 you get YELLOW, you need to use BRGW (note that BRG is only supported in the latest Klipper
#                 version).
#
#     4.  Once you have confirmed that the LEDs are set up correctly, you must now decide where you want 
#         these macros called up...which means adding them to your existing gcode macros.  NOTHING will happen
#         unless you add the STATUS_????? macros to your existing gcode macros.  
#
#           Example: add STATUS_LEVELING to the beginning of your QGL gcode macro, and then add STATUS_READY 
#                    to the end of it to set the logo LED and nozzle LEDs back to the `ready` state.
#
#           Example: add STATUS_CLEANING to the beginning of your nozzle-cleaning macro, and then STATUS_READY
#                    to the end of it to return the LEDs back to `ready` state.
#
#     5.  Feel free to change colors of each macro, create new ones if you have a need to.  The macros provided below
#         are just an example of what is possible.  If you want to try some more complex animations, you will most
#         likely have to use WLED with Moonraker and a small micro-controller (please see the LED thread for help inside
#         of the stealthburner_beta channel on Discord).
#
#####################################
#       END INSTRUCTRUCTIONS        #
#####################################


[neopixel sb_leds]
pin: PB0
#   The pin connected to the neopixel. This parameter must be provided.
chain_count: 10
#   The number of Neopixel chips that are "daisy chained" to the
#   provided pin. The default is 1 (which indicates only a single
#   Neopixel is connected to the pin).
color_order: GRB, GRB, GRB, GRB, GRB, GRB, GRB, GRB, GRBW,  GRBW
#   Set the pixel order required by the LED hardware. Options are GRB,
#   RGB, GRBW, or RGBW. The default is GRB.
initial_RED: 1.0
initial_GREEN: 0.0
initial_BLUE: 1.0
initial_WHITE: 0.0
#   Sets the initial LED color of the Neopixel. Each value should be
#   between 0.0 and 1.0. The WHITE option is only available on RGBW
#   LEDs. The default for each color is 0.#


##########################
# LED Effects Animations #
##########################

##################
## logo effects ##
##################

[led_effect sb_logo_busy]
autostart:              false
frame_rate:             24
leds:
    neopixel:sb_leds (1-8)
layers:
    breathing  3 1 top (1,0,0)

[led_effect sb_logo_cleaning]
autostart:              false
frame_rate:             24
leds:
    neopixel:sb_leds (1-8)
layers:
    breathing  3 1 top (0.0, 0.02, 0.5)

[led_effect sb_logo_calibrating_z]
autostart:              false
frame_rate:             24
leds:
    neopixel:sb_leds (1-8)
layers:
        breathing  3 1 top (0.0, 0.0, 0.35)

[led_effect sb_logo_heating]
leds:
    neopixel:sb_leds (1,3,7,8,6,2)
autostart:                          false
frame_rate:                         24
layers:
    comet  0.3  0 add (1, 0.18, 0)

[led_effect sb_logo_cooling]
leds:
    neopixel:sb_leds (1,3,7,8,6,2)
autostart:                          false
frame_rate:                         24
layers:
    comet  0.3  0 add (0, 0, 1)

[led_effect sb_logo_homing]
autostart:              false
frame_rate:             24
leds:
    neopixel:sb_leds (1-8)
layers:
        breathing  3 1 top (0.0, 0.6, 0.2)

[led_effect sb_logo_leveling]
autostart:              false
frame_rate:             24
leds:
    neopixel:sb_leds (1-8)
layers:
        breathing  3 1 top (0.5, 0.1, 0.4)

[led_effect sb_logo_meshing]
autostart:              false
frame_rate:             24
leds:
    neopixel:sb_leds (1-8)
layers:
        breathing  3 1 top (0.2, 1.0, 0.0)

[led_effect sb_logo_printing]
autostart:              false
frame_rate:             24
leds:
    neopixel:sb_leds (1-8)
layers:
    gradient  0.3  1 add (0.3, 0.0, 0.0),(0.3, 0.3, 0.0),(0.3, 0.1, 0.0)

[led_effect sb_logo_standby]
autostart:              false
frame_rate:             24
leds:
    neopixel:sb_leds (1-8)
layers:
        breathing  3 1 top (0.01, 0.01, 0.01)

[led_effect sb_logo_part_ready]
autostart:              false
frame_rate:             24
leds:
    neopixel:sb_leds (1-8)
layers:
        breathing  3 1 top (0.0, 1.0, 0.0)

####################
## nozzle effects ##
####################

[led_effect sb_nozzle_heating]
autostart:              false
frame_rate:             24
leds:
    neopixel:sb_leds (9,10)
layers:
        breathing  3 1 top (1.0, 0.18, 0.0, 0.0)

[led_effect sb_nozzle_cooling]
autostart:              false
frame_rate:             24
leds:
    neopixel:sb_leds (9,10)
layers:
        breathing  3 1 top (0.0, 0.0, 1.0, 0.1)

[led_effect sb_nozzle_standby]
autostart:              false
frame_rate:             24
leds:
    neopixel:sb_leds (9,10)
layers:
        breathing  3 1 top (0.6, 0.0, 0.0, 0.0)

[led_effect sb_nozzle_part_ready]
autostart:              false
frame_rate:             24
leds:
    neopixel:sb_leds (9,10)
layers:
        breathing  3 1 top (0.6, 1.0, 0.0, 0.1)


#####################
## all led effects ##
#####################

[led_effect sb_critical_error]
leds:
    neopixel:sb_leds
layers:
    strobe         1  1.5   add        (1.0,  1.0, 1.0)
    breathing      2  0     difference (0.95, 0.0, 0.0)
    static         1  0     top        (1.0,  0.0, 0.0)
autostart:                             false
frame_rate:                            24
run_on_error:                          true


[led_effect rainbow]
leds:
    neopixel:sb_leds
autostart:                          true
frame_rate:                         24
layers:
    gradient  0.3  1 add (0.3, 0.0, 0.0),(0.0, 0.3, 0.0),(0.0, 0.0, 0.3)


#######################
# LED Effects Statics #
#######################

[led_effect set_nozzle_leds]
leds:
    neopixel:sb_leds (9,10)
   #neopixel:caselight
autostart:                          false
frame_rate:                         24
layers:
    static         0  0     top        (0.0,  0.0, 0.0, 1.0)

[led_effect set_logo_leds]
leds:
    neopixel:sb_leds (1,2,3,4,5,6,7,8)
   #neopixel:caselight
autostart:                          false
frame_rate:                         24
layers:
    static         0  0     top        (1.0,  1.0, 1.0)

##############
# The Macros #
##############

[gcode_macro set_logo_leds_off]
gcode:
    SET_LED_EFFECT EFFECT=set_logo_leds STOP=1

[gcode_macro set_logo_leds_on]
gcode:
    SET_LED_EFFECT EFFECT=set_logo_leds

[gcode_macro set_nozzle_leds_on]
gcode:
    SET_LED_EFFECT EFFECT=set_nozzle_leds

[gcode_macro set_nozzle_leds_off]
gcode:
    SET_LED_EFFECT EFFECT=set_nozzle_leds STOP=1

[gcode_macro status_off]
gcode:
    STOP_LED_EFFECTS

[gcode_macro status_ready]
gcode:
    STOP_LED_EFFECTS
    SET_LED_EFFECT EFFECT=rainbow

[gcode_macro status_part_ready]
gcode:
    STOP_LED_EFFECTS
    SET_LED_EFFECT EFFECT=sb_nozzle_part_ready
    SET_LED_EFFECT EFFECT=sb_logo_part_ready

[gcode_macro status_busy]
gcode:
    STOP_LED_EFFECTS
    SET_LED_EFFECT EFFECT=sb_logo_busy
    set_nozzle_leds_on

[gcode_macro status_heating]
gcode:
    STOP_LED_EFFECTS
    SET_LED_EFFECT EFFECT=sb_logo_heating
    SET_LED_EFFECT EFFECT=sb_nozzle_heating
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

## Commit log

2023-12-06 Adds `generated_bom.csv` and updated `voron_2_tall_bom.xlsx`.
    [generated_bom.csv, voron_2_tall_bom.xlsx]
2023-12-09 Updates BOM to link to correct acrylic sheet size and adds printed parts list.
    [voron_2_tall_bom.xlsx]
2023-12-23 Adds Manuals and STL files from mods githubs.
    [Dock_mount_fixed_v2.stl, Dock_mount_variable_pt1_v2.stl, Dock_mount_variable_pt2_v2.stl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]
2024-01-01 Adds Manuals and additional printed parts.
    [LED_Bar_Clip_Misumi_version2.stl, MGN12_rail_guide_x2.stl, MGN9_rail_guide_x2.stl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]
2024-01-06 Adds updates to githubs and printed parts.
    [2020_Mount.stl, 2020_Mount_Mirrored.stl, 3030_Flat_Mount.stl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]
2024-01-06 Adds modified 350 panels to `Drawing_DXFs`.
    [350_Back_Panel.SLDPRT, 350_Back_Panel_Vanilla.DXF, 350_Back_Panel_Vanilla.SLDPRT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]
2024-01-11 Updates BOM and adds more `STL` files to `Printed_Parts`.
    [LDO_bed_wago_mount.stl, LDO_beefy_raspberry_bracket.stl, LDO_mount.stl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]
2024-01-16 Adds purge bucket to printed parts.
    [brush_holder_sheet_stop.stl, individual_sheet_stop.stl, purge_bucket_350mm_rev4.stl]
2024-01-18 Adds `350_Side_Panel_Handles` designs.
    [350_Side_Panel_Handles.DXF, 350_Side_Panel_Handles.SLDPRT]
2024-01-19 Updates `350_Side_Panel_Handles.DXF` dimensions.
    [350_Side_Panel_Handles.DXF, 350_Side_Panel_Handles.SLDPRT]
2024-01-21 Updates dimensions of handles.
    [350_Side_Panel_Handles.DXF, 350_Side_Panel_Handles.SLDPRT]
2024-01-24 Adds and renames printed part quantities and updates BOM.
    [LED_Bar_Clip_Misumi_version2_x24.stl, [a]_side_skirt_a_350_insert.stl, bottom_panel_clip_x4.stl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]
2024-01-28 Adds `.cdr` files for panels and reorganizes related files.
    [250_Back_Panel.DXF, 250_Bottom_Panel.dxf, 250_Deck_Panel.dxf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]
2024-01-28 Renames panel files and updates `README.md`.
    [Back_Panel.DXF, Back_Panel.SLDPRT, Bottom_Panel.dxf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]
2024-02-11 Updates `BOM` with more parts, adds print ready panels, and used `.stl`s.
    [Filament_Card.stl, Filament_Card_Caddy_25.stl, Heatset_Practice.stl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]
2024-05-04 Removes unused stl parts for XY_Joints and Stealtburner.
    [[a]_endstop_pod_hall_effect.stl, cable_cover_pcb.stl, cable_cover_pcb_with_thermistor.stl]
2024-05-04 Starts work on handle cover.
    [Handle_Cover.SLDPRT, Handle_Cover.STL]
2024-05-04 Adds changes to Handle Cover.
    [Handle_Cover.SLDPRT, Handle_Cover.STL]
2024-05-19 Updates BOM and adds more githubs.
    [Cowl_NoProbe.stl, voron_2_tall_bom.xlsx]
2024-05-25 Adds mods and printed parts.
    [2020_Mount.stl, 2020_Mount_Mirrored.stl, 3030_Flat_Mount.stl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]
2024-05-29 Updates BOM with dragon burner toolhead links.
    [Brace_Straight.stl, Cowl_NoProbe.stl, Gear_Housing_65_teeth.stl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]
2024-06-01 Adds updates for canbus setup in `README.md`
2024-06-01 Updates `README.md` with Toolhead section.
2024-06-30 Updates firmware files.
    [ebb-canbus-v1.2.cfg, stealthburner_led_effects_barf.cfg, voron_2_tall_bom.xlsx]
